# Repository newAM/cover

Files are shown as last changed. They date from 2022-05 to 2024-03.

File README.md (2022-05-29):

# Cover

A controller to automate my window shades.

This project is from late 2020; much older than the commit dates indicate.  I revisited it to migrate the raspberry pi controller to NixOS and decided to document the project.

## Software

* [NixOS](https://nixos.org/) for the raspberry pi OS
* [KiCad](https://www.kicad.org/) (version 5) for PCB design
* [OpenSCAD](https://openscad.org/) for 3D printed parts

## Hardware

The hardware consists of:

* A raspberry pi
* A custom pi hat to drive motors
* A motor per shade
* Plastic 3D printed motor mounts
* Metal 3D printed grips
* Plastic 3D printed guides
* 2 reed switches on each shade for endstops

### Shades

The shades on my windows have a continuous ball chain string without any clasps.  The ball chain originally had some plastic stoppers on them, but these all broke off before this project due to UV exposure.

The windows have a clutch on them, I measured the force required to overcome this clutch by tieing a water bottle onto the ball chain, and filling it with water until the chain started to move.  The final weight of the water bottle was 2 kilos ∴ about 20N of force is required to move the shades.

### Motors

I purchased generic 12V motors online, if you search "DC 12V worm gear motor" you will find these easily at almost every retailer.  These had more than enough torque to overcome the 20N of the clutch.

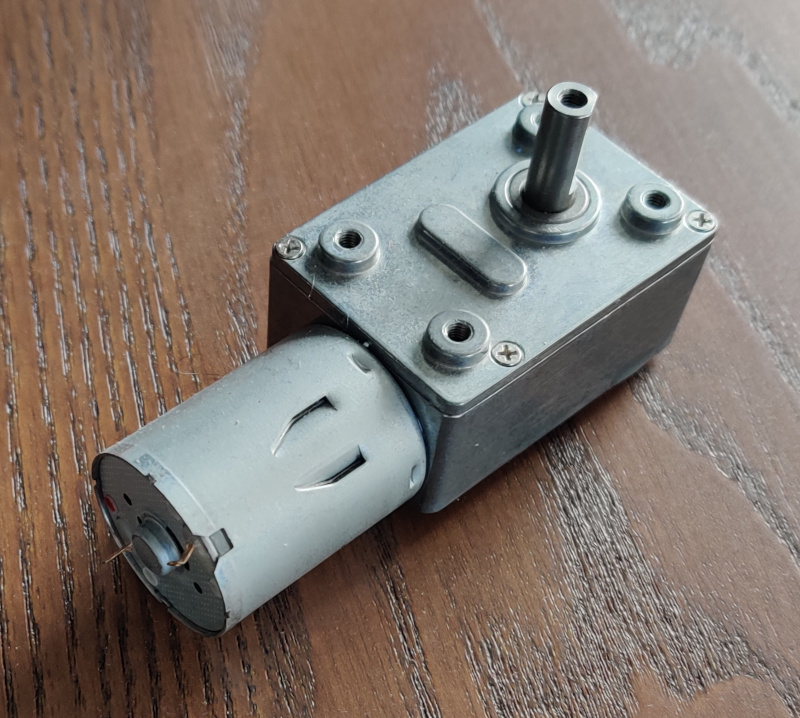
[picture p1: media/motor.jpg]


I purchased 25 rpm motors, which was lower than I needed.  The grips ended up being a smaller diameter than I initially intended; which means the shades move slower than intended.

#### Grips

The grip is a metal 3D printed part with grooves for the ball chain.  I tried to make this in plastic, but the forces required always stripped plastic parts.

The intent was to make this part match the diameter of the clutch on my shades, but metal 3D printing is extremely expensive, and I ended up making the part much smaller to keep costs down.  Each part ended up costing $40 from [shapeways](https://www.shapeways.com/).

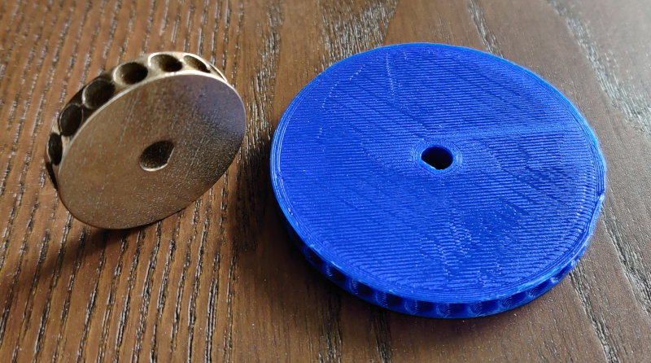
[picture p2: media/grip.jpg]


#### Mount

The mount screws onto the motor and has two large flat surfaces to mount the motor onto the wall with command strips.  I used command strips because I rent, but they were probably the best solution anyway.

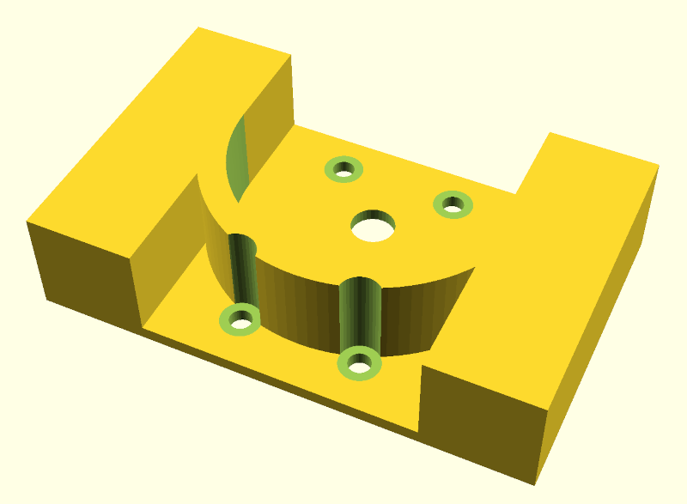
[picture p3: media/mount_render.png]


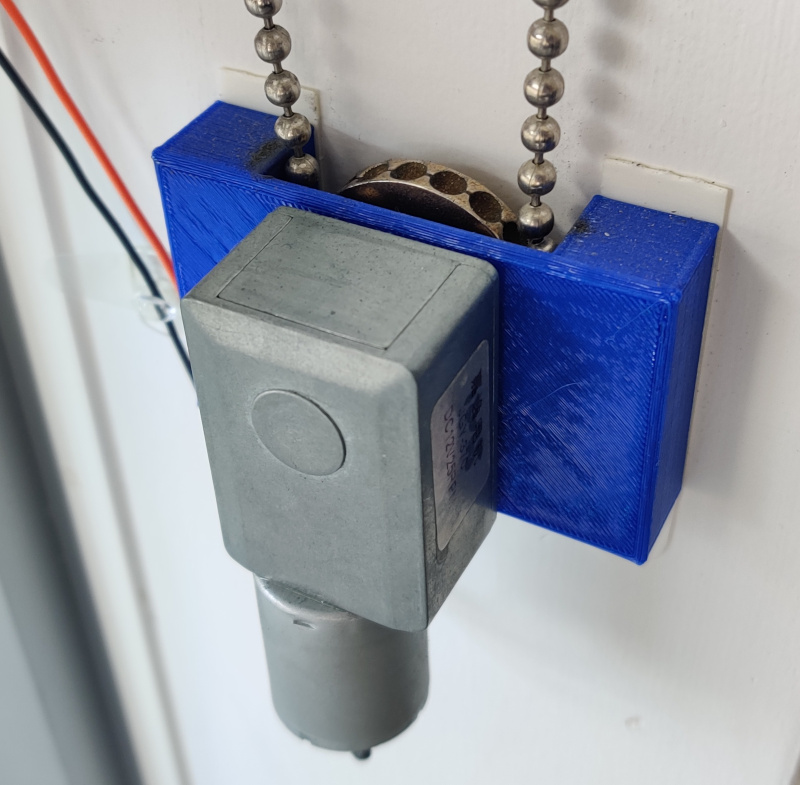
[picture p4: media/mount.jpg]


### Endstops

The endstops consisted of two reed switches per window, one at the top of the frame, and one at the bottom.  I taped magnets onto the shades to trip the reed switches when the shades hit the limit.

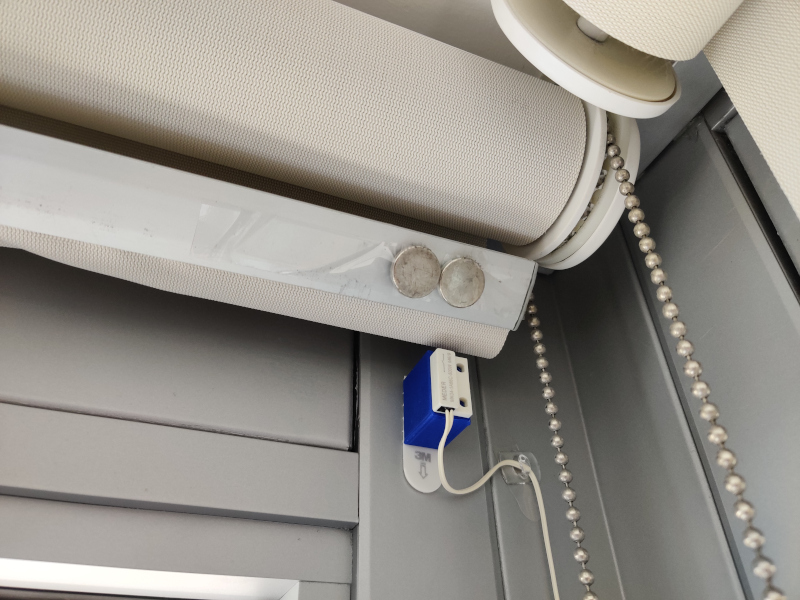
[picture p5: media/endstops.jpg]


3D printed mounts were necessary to raise the reed switches to the shades.

### Controller

The controller is just a hat on a raspberry pi with 6x inputs for reed switches, and 3x DRV8871DDAR motor drivers for the output.

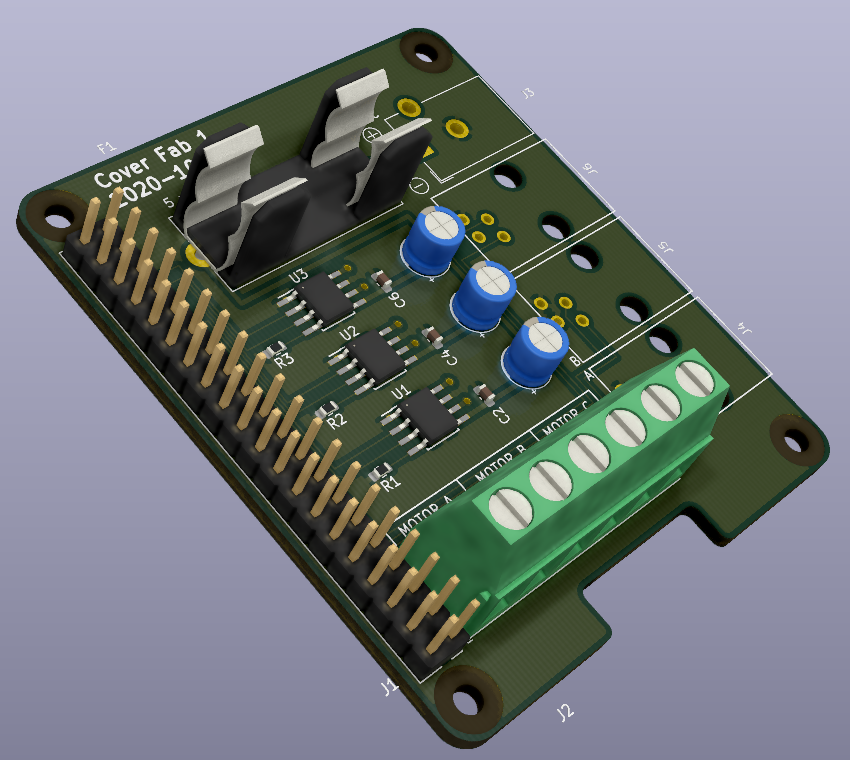
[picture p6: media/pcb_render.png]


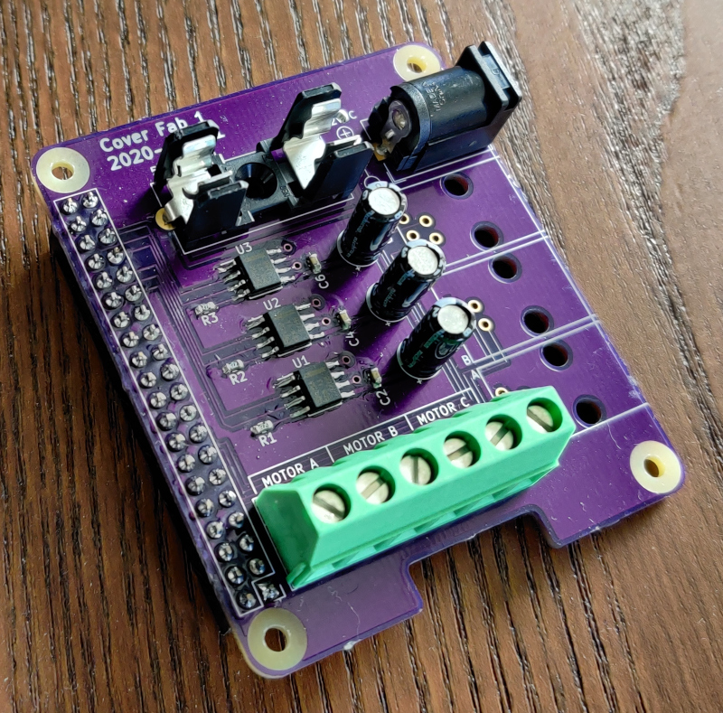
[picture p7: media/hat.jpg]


If I had to do this project over I would have used an Ethernet connected microcontroller instead of a pi.  Upon boot the raspberry pi takes a few seconds to apply the GPIO configuration in `/boot/config.txt`, which is not desirable, as this can lead to the shades moving beyond their endstop positions.

The controller takes commands over MQTT for move up, move down, and stop.

I run [NixOS](https://nixos.org/) on the pi.  The only other configuration necessary is putting `gpio=5,12,6,13,19,16=op,dl` into `/boot/config.txt`:

```nix
{
  boot.loader.raspberryPi = {
    enable = true;
    version = n;
    firmwareConfig = ''
      gpio=5,12,6,13,19,16=op,dl
    '';
  };
}
```

The service is a simple python script that I am not very proud of because it is all blocking code with polling.  I plan to rewrite this at some point, but it keeps working so I keep putting it off.

## Home Assistant

Home-assistant has a [MQTT cover integration](https://www.home-assistant.io/integrations/cover.mqtt/) that works out of the box.

```nix
{
  services.home-assistant.config.cover = [
    {
      platform = "mqtt";
      name = "Middle Window";
      unique_id = "middle_window";
      command_topic = "/home/sunroom/middle_window/set";
      position_topic = "/home/sunroom/middle_window/position";
      optimistic = false;
      retain = false;
    }
    # ... other shades
  ];
}
```

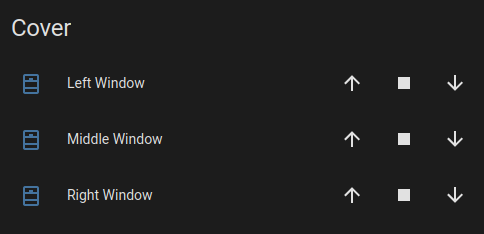
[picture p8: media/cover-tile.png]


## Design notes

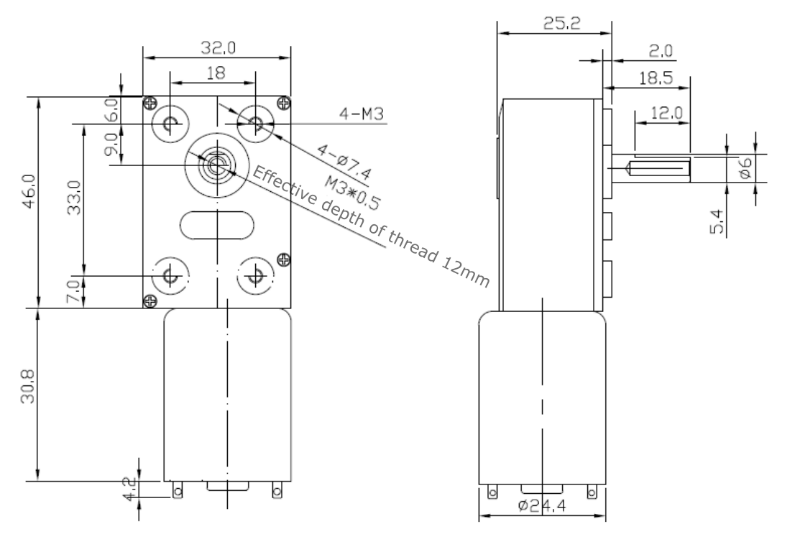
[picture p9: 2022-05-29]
media/motor_dimensions.png

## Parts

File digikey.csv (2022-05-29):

Index | Quantity | Part Number | Manufacturer Part Number | Description | Customer Reference | Available | Backorder | Unit Price | Extended Price CAD
1 | 2 | 277-8599-ND | 1715190 | TERM BLK 6POS SIDE ENTRY 5MM PCB |  | 2 | 0 | 5.26000 | 10.52
2 | 6 | 296-43024-1-ND | DRV8871DDAR | IC MOTOR DRVR UNIPLR 8SO PWRPAD |  | 6 | 0 | 3.86000 | 23.16
3 | 6 | 493-1121-ND | UVR1J220MDD | CAP ALUM 22UF 20% 63V RADIAL |  | 6 | 0 | 0.32000 | 1.92
4 | 10 | 1276-1934-1-ND | CL10B104KB8NFNC | CAP CER 0.1UF 50V X7R 0603 |  | 10 | 0 | 0.04000 | 0.40
5 | 2 | 486-1258-ND | 0031.8201 | FUSE BLOK CARTRIDGE 500V 10A PCB |  | 2 | 0 | 1.40000 | 2.80
6 | 2 | 507-1227-ND | 5SF 1.6-R | FUSE GLASS 1.6A 250VAC 5X20MM |  | 2 | 0 | 0.35000 | 0.70
7 | 2 | CP-102AH-ND | PJ-102AH | CONN PWR JACK 2X5.5MM SOLDER |  | 2 | 0 | 1.10000 | 2.20
8 | 12 | AE11234-ND | A-20040 | CONN MOD JACK 4P4C R/A UNSHLD |  | 12 | 0 | 0.95800 | 11.50
9 | 25 | AE10314-ND | A-MO 4/4 F50 | CONN MOD PLUG 4P4C UNSHIELDED |  | 25 | 0 | 0.19880 | 4.97
10 | 2 | Q1182-ND | QFWB-30-12-US01 | AC/DC WALL MOUNT ADAPTER 12V 30W |  | 2 | 0 | 12.92000 | 25.84
11 | 2 | S7123-ND | PPPC202LFBN-RC | CONN HDR 40POS 0.1 GOLD PCB |  | 2 | 0 | 3.44000 | 6.88
12 | 2 | 507-1246-ND | 5ST 1-R | FUSE GLASS 1A 250VAC 5X20MM |  | 2 | 0 | 0.35000 | 0.70
13 | 2 | 507-1248-ND | 5ST 1.6-R | FUSE GLASS 1.6A 250VAC 5X20MM |  | 2 | 0 | 0.35000 | 0.70
14 | 10 | 469-1039-ND | 8110 | MAGNET 1" L X 0.25" W RECT |  | 10 | 0 | 1.22000 | 12.20
15 | 10 | 311-27.0KHRCT-ND | RC0603FR-0727KL | RES SMD 27K OHM 1% 1/10W 0603 |  | 10 | 0 | 0.03200 | 0.32
16 | 10 | 311-4.70KHRCT-ND | RC0603FR-074K7L | RES SMD 4.7K OHM 1% 1/10W 0603 |  | 10 | 0 | 0.03200 | 0.32

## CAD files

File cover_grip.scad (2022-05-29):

HEIGHT = 6;
STRING_RADIUS = 0.6;
SHAFT_RADIUS = 3;
FLAT_RADIUS = 2.4;
BEAD_RADIUS = 2.4;
BEAD_GAP = 0.2;
BEAD_SPACING = 6;
NUM_BEADS = 18;

CIRCUMFERENCE = NUM_BEADS * BEAD_SPACING;
RADIUS = CIRCUMFERENCE / (2 * PI);
ANGLE_SPACING = 360 / NUM_BEADS;

echo(CIRCUMFERENCE=CIRCUMFERENCE);
echo(RADIUS=RADIUS);
echo(ANGLE_SPACING=ANGLE_SPACING);

module bead_holes()
{
    fn = 36;
    hole_size = BEAD_RADIUS + BEAD_GAP;
    cyl_radius = RADIUS + hole_size;

    // repeat bead holes
    for (theta=[0:ANGLE_SPACING:360])
    {
        union()
        {
            // cylindrical to Cartesian coordinate conversion
            translate([RADIUS * cos(theta), RADIUS * sin(theta), 0])
            {
                // bead hole
                sphere(hole_size, $fn=fn);
            }
            translate([cyl_radius * cos(theta), cyl_radius * sin(theta), 0])
            {
                rotate([-theta, 90, 0])
                {
                    cylinder(r=hole_size, h=hole_size, $fn=fn);
                }
            }
        }
    }
}

difference()
{
    // body
    cylinder(h=HEIGHT, r1=RADIUS, r2=RADIUS, center=true, $fn=180);

    bead_holes();

    // string cutout
    difference()
    {
        linear_extrude(height=STRING_RADIUS+BEAD_GAP, center=true)
        {
            difference()
            {
                circle(r=RADIUS+0.001, $fn=180);
                circle(r=RADIUS-STRING_RADIUS+BEAD_GAP, $fn=180);
            }
        }
        bead_holes();
    }

    // shaft
    linear_extrude(height=HEIGHT+1, center=true)
    {
        scale(1.1)
        {
            difference()
            {
                circle(r=SHAFT_RADIUS, $fn=90);

                // "D" shape
                translate([FLAT_RADIUS + SHAFT_RADIUS, 0, 0])
                {
                    square([SHAFT_RADIUS * 2, SHAFT_RADIUS * 2], center=true);
                }
            }
        }
    }
}

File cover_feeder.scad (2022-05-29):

GEARBOX_WIDTH = 32;
GEARBOX_DEPTH = 46;
GEARBOX_HEIGHT = 25.2;

GEARBOX_GAP = 1;

SCREW_HOLE_HEIGHT = 2;
SCREW_HOLE_X_OFFSET = 9;
SCREW_HOLE_Y_OFFSET_TOP = 17;
SCREW_HOLE_Y_OFFSET_BOTTOM = 16;

CASE_WALL_THICKNESS = 2;
GAP_SIZE = 0.3;  // gap between motor and housing

SHAFT_Y_OFFSET = 8;
SHAFT_DIAMETER = 6;
SHAFT_LENGTH = 14;
SHAFT_CLEARANCE = 2;

M3_HOLE_DIAMETER = 3.3;
M3_SCREW_HEAD_DIAMETER = 6;

GRIP_DIAMETER = 41;
GRIP_GUIDE_WALL_THICKNESS = 4;
GRIP_GUIDE_DEPTH = 12;
GRIP_GUIDE_HEIGHT = SHAFT_LENGTH - CASE_WALL_THICKNESS + SHAFT_CLEARANCE;
GRIP_OD = GRIP_DIAMETER + GRIP_GUIDE_WALL_THICKNESS * 2;

COMMAND_STRIP_LENGTH = 46;
COMMAND_STRIP_WIDTH = 16;

module m3_cutout()
{
    cylinder(
        h=CASE_WALL_THICKNESS + 0.001,
        d=M3_HOLE_DIAMETER,
        center=true,
        $fn=36
    );
    translate([0, 0, CASE_WALL_THICKNESS / 2 + GRIP_GUIDE_HEIGHT / 2])
    {
        cylinder(
            h=GRIP_GUIDE_HEIGHT + 0.001,
            d=M3_SCREW_HEAD_DIAMETER,
            center=true,
            $fn=36
        );
    }
}

module feeder()
{
    union()
    {
        difference()
        {
            // ring
            cylinder(
                h=GRIP_GUIDE_HEIGHT,
                d=GRIP_OD,
                $fn=100,
                center=true
            );
            cylinder(h=GRIP_GUIDE_HEIGHT+0.001, d=GRIP_DIAMETER, $fn=100, center=true);

            // half-cylinder
            translate([0, GRIP_OD / 2, 0])
            {
                cube(GRIP_OD, center=true);
            }

        }

        // straight portion
        for (x=[1, -1])
        {
            translate(
                [
                    (GRIP_DIAMETER / 2 + GRIP_GUIDE_WALL_THICKNESS / 2) * x,
                    GRIP_GUIDE_DEPTH / 2,
                    0,
                ]
            )
            {
                cube(
                    [
                        GRIP_GUIDE_WALL_THICKNESS,
                        GRIP_GUIDE_DEPTH,
                        GRIP_GUIDE_HEIGHT
                    ],
                    center=true
                );
            }
        }
    }
}

difference()
{
    base_width = GRIP_DIAMETER + COMMAND_STRIP_WIDTH * 2;

    union()
    {
        cube(
            [
                base_width,
                GEARBOX_DEPTH,
                CASE_WALL_THICKNESS
            ],
            center=true
        );
        translate(
            [
                0,
                SHAFT_Y_OFFSET,
                CASE_WALL_THICKNESS / 2 + GRIP_GUIDE_HEIGHT / 2
            ]
        )
        {
            feeder();
        }

        for (x=[1, -1])
        {
            translate(
                [
                    x * ((GRIP_DIAMETER + COMMAND_STRIP_WIDTH) / 2),
                    0,
                    (CASE_WALL_THICKNESS + GRIP_GUIDE_HEIGHT) / 2,
                ]
            )
            {
                cube(
                    [COMMAND_STRIP_WIDTH, COMMAND_STRIP_LENGTH, GRIP_GUIDE_HEIGHT],
                    center=true
                );
            }
        }
    }
    translate([0, SHAFT_Y_OFFSET, 0])
    {
        cylinder(
            h=CASE_WALL_THICKNESS + 0.001,
            d=SHAFT_DIAMETER + GAP_SIZE * 2,
            center=true,
            $fn=36
        );
    }
    for (x=[1, -1])
    {
        translate([x*SCREW_HOLE_X_OFFSET, SCREW_HOLE_Y_OFFSET_TOP, 0])
        {
            m3_cutout();
        }
        translate([x*SCREW_HOLE_X_OFFSET, -SCREW_HOLE_Y_OFFSET_BOTTOM, 0])
        {
            m3_cutout();
        }
    }
}

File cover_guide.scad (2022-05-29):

WIDTH = 17;
LENGTH = 60;
HEIGHT = 60;

difference() {
    cylinder(WIDTH, LENGTH, LENGTH, $fn=3, center=false);
    translate([-100, 0, -0.001]) {
        cube([LENGTH * 100, LENGTH * 100, LENGTH * 100]);
    }
}

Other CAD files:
reed_holder.scad

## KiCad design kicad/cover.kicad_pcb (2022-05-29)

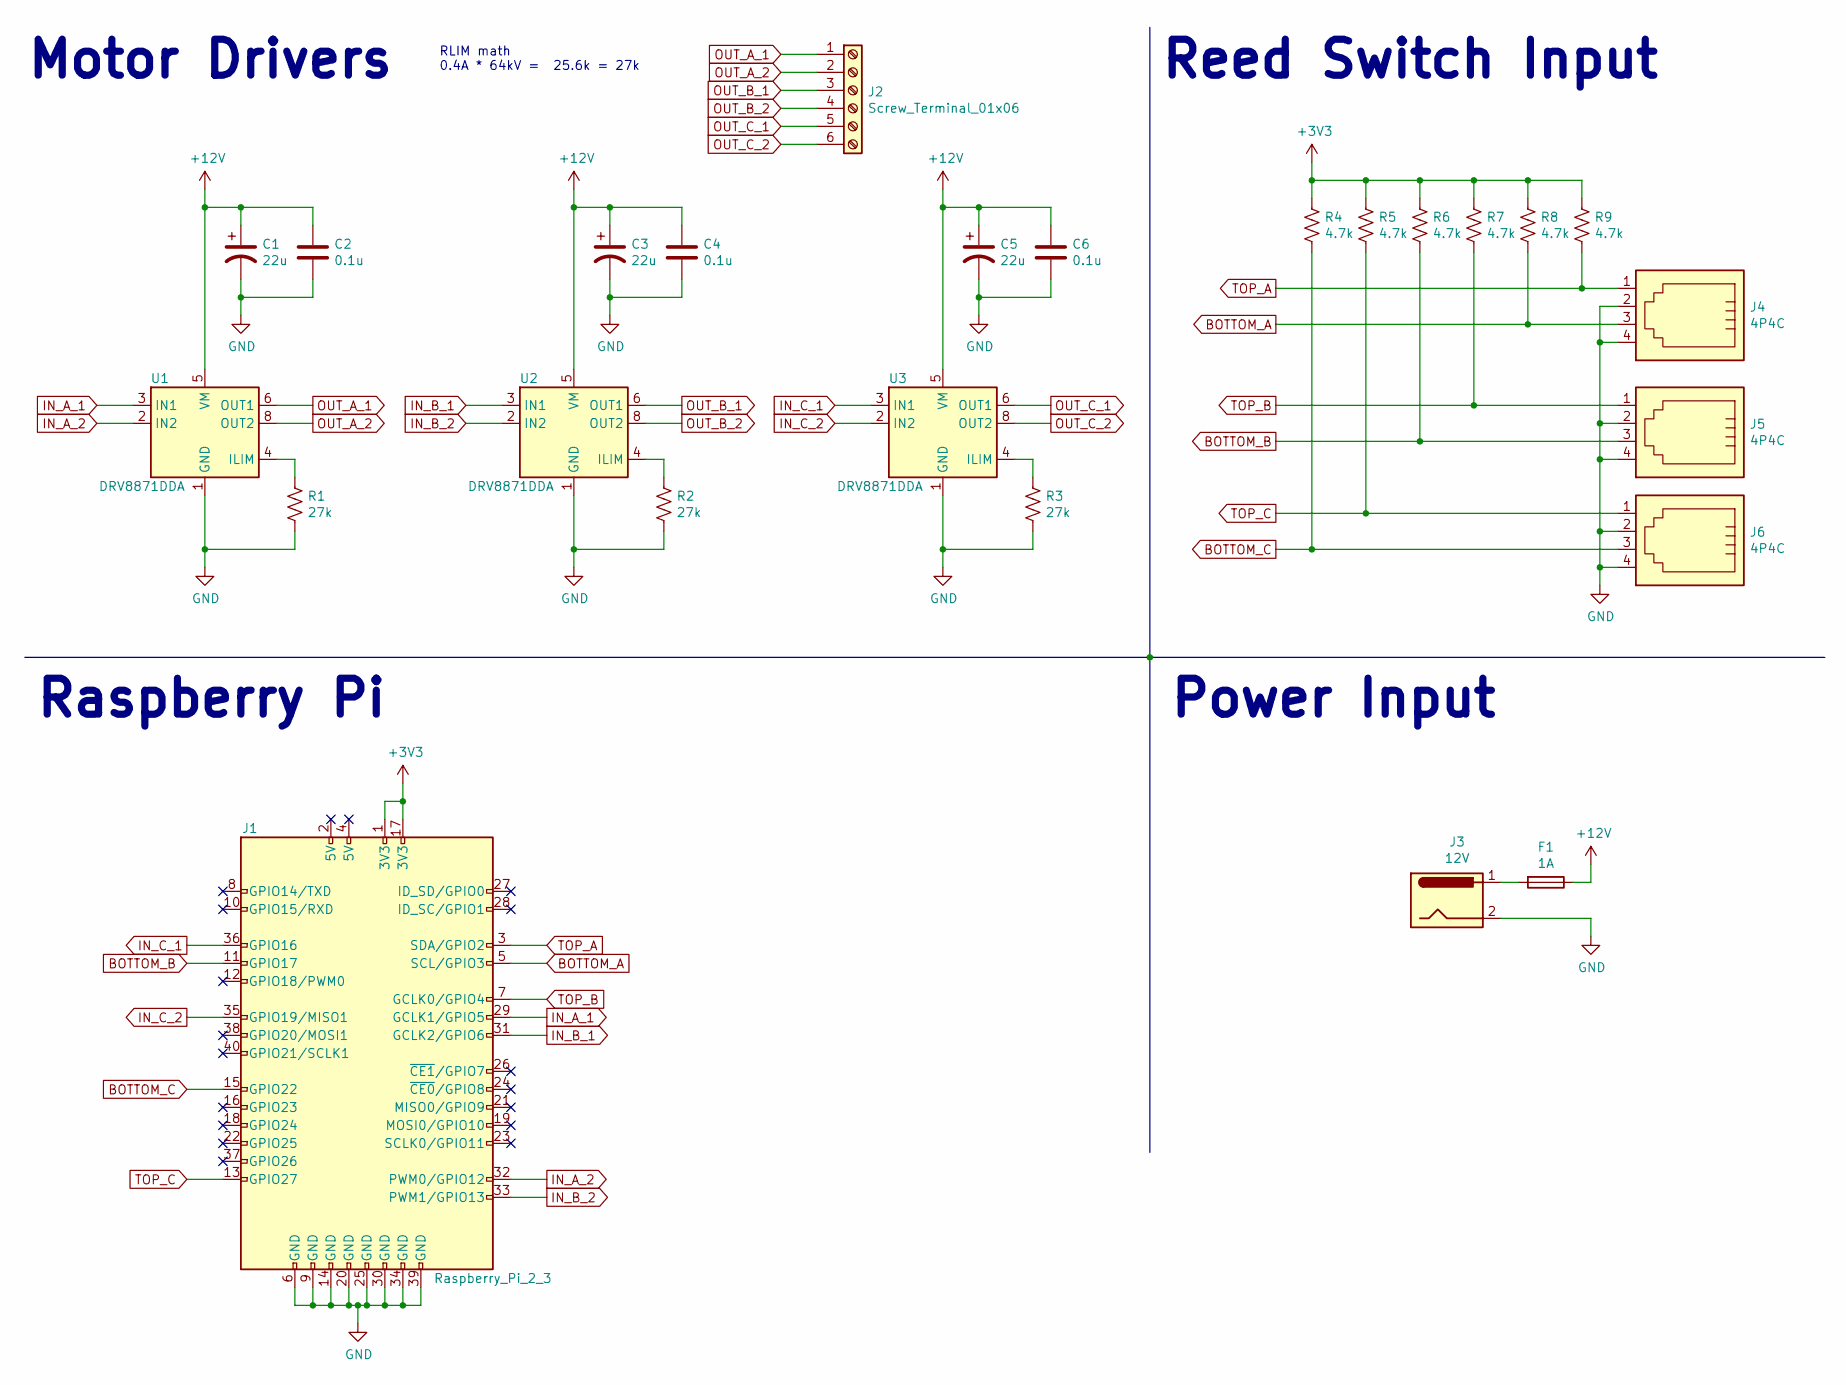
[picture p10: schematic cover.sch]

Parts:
C1, C3, C5: 22u; CP_Radial_D5.0mm_P2.00mm
C2, C4, C6: 0.1u; C_0603_1608Metric
F1: 1A; Fuseholder_Cylinder-5x20mm_Schurter_0031_8201_Horizontal_Op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
J1: Raspberry_Pi_2_3; PinHeader_2x20_P2.54mm_Vertical
J2: Screw_Terminal_01x06; TerminalBlock_Phoenix_MKDS-1,5-6_1x06_P5.00mm_Horizontal
J3: 12V; BarrelJack_CUI_PJ-102AH_Horizontal
J4, J5, J6: 4P4C; A-2004-3-4-LP-N-R
R1, R2, R3: 27k; R_0603_1608Metric
R4, R5, R6, R7, R8, R9: 4.7k; R_0603_1608Metric
U1, U2, U3: DRV8871DDA; Texas_HTSOP-8-1EP_3.9x4.9mm_P1.27mm_EP2.95x4.9mm_Mask2.4x3.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

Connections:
+3V3: J1.1 (3V3), J1.17 (3V3), R4.1, R5.1, R6.1, R7.1, R8.1, R9.1
+12V: C1.1, C2.1, C3.1, C4.1, C5.1, C6.1, F1.1, U1.5 (VM), U2.5 (VM), U3.5 (VM)
BOTTOM_A: J1.5 (SCL/GPIO3), J4.3, R8.2
BOTTOM_B: J1.11 (GPIO17), J5.3, R6.2
BOTTOM_C: J1.15 (GPIO22), J6.3, R4.2
GND: C1.2, C2.2, C3.2, C4.2, C5.2, C6.2, J1.6 (GND), J1.9 (GND), J1.14 (GND), J1.20 (GND), J1.25 (GND), J1.30 (GND), J1.34 (GND), J1.39 (GND), J3.2, J4.2, J4.4, J5.2, J5.4, J6.2, J6.4, R1.2, R2.2, R3.2, U1.1 (GND), U1.7 (GND), U1.9 (GND), U2.1 (GND), U2.7 (GND), U2.9 (GND), U3.1 (GND), U3.7 (GND), U3.9 (GND)
IN_A_1: J1.29 (GCLK1/GPIO5), U1.3 (IN1)
IN_A_2: J1.32 (PWM0/GPIO12), U1.2 (IN2)
IN_B_1: J1.31 (GCLK2/GPIO6), U2.3 (IN1)
IN_B_2: J1.33 (PWM1/GPIO13), U2.2 (IN2)
IN_C_1: J1.36 (GPIO16), U3.3 (IN1)
IN_C_2: J1.35 (GPIO19/MISO1), U3.2 (IN2)
unnamed: F1.2, J3.1
unnamed: R1.1, U1.4 (ILIM)
unnamed: R2.1, U2.4 (ILIM)
unnamed: R3.1, U3.4 (ILIM)
OUT_A_1: J2.1, U1.6 (OUT1)
OUT_A_2: J2.2, U1.8 (OUT2)
OUT_B_1: J2.3, U2.6 (OUT1)
OUT_B_2: J2.4, U2.8 (OUT2)
OUT_C_1: J2.5, U3.6 (OUT1)
OUT_C_2: J2.6, U3.8 (OUT2)
TOP_A: J1.3 (SDA/GPIO2), J4.1, R9.2
TOP_B: J1.7 (GCLK0/GPIO4), J5.1, R7.2
TOP_C: J1.13 (GPIO27), J6.1, R5.2

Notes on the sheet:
RLIM math 0.4A * 64kV = 25.6k = 27k
Motor Drivers
Reed Switch Input
Raspberry Pi
Power Input

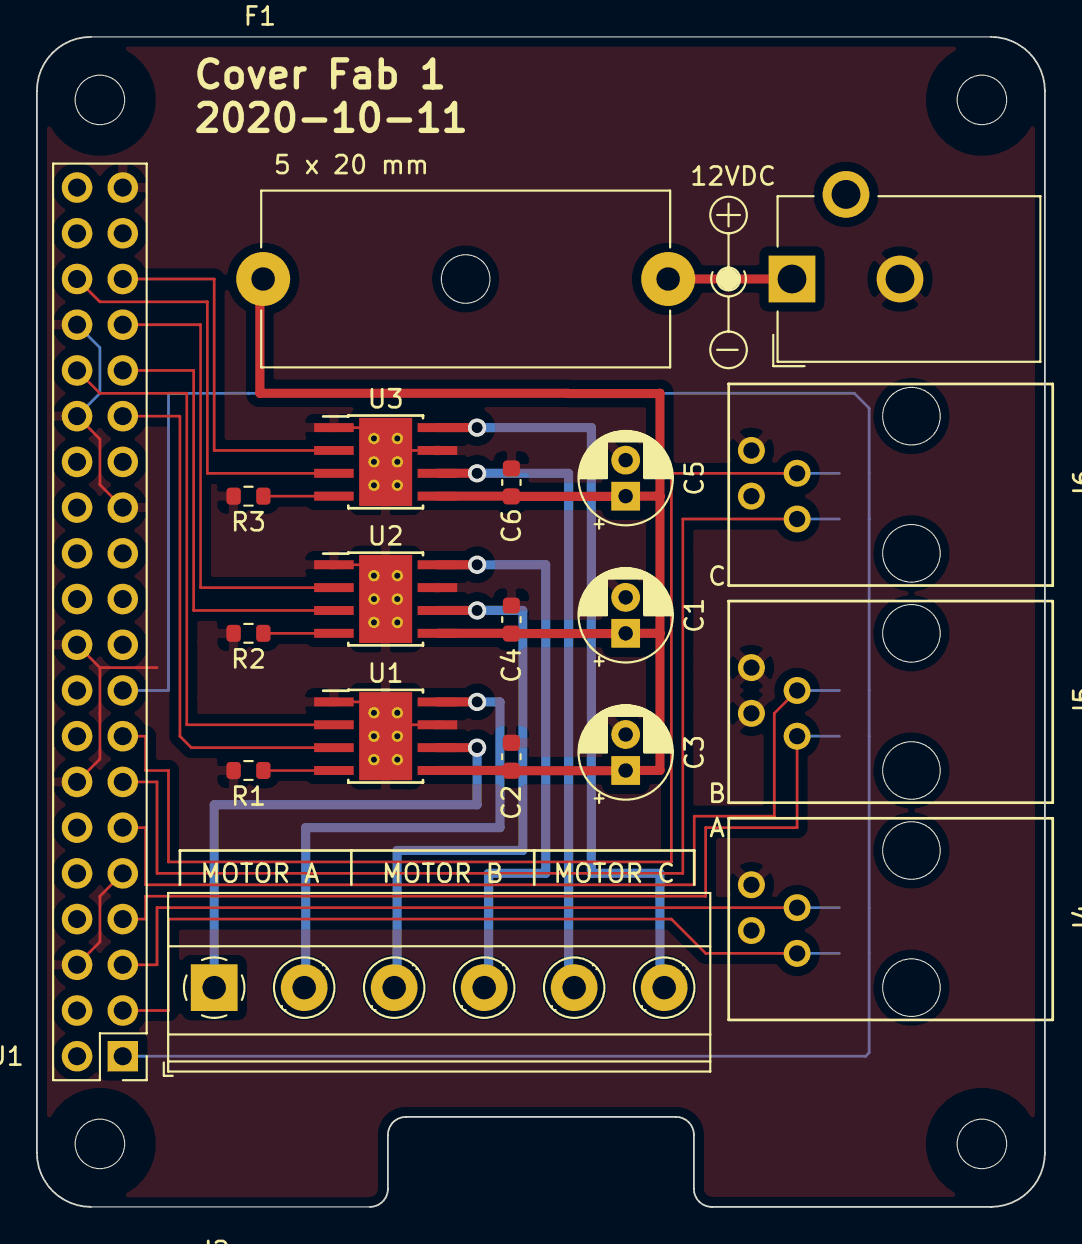
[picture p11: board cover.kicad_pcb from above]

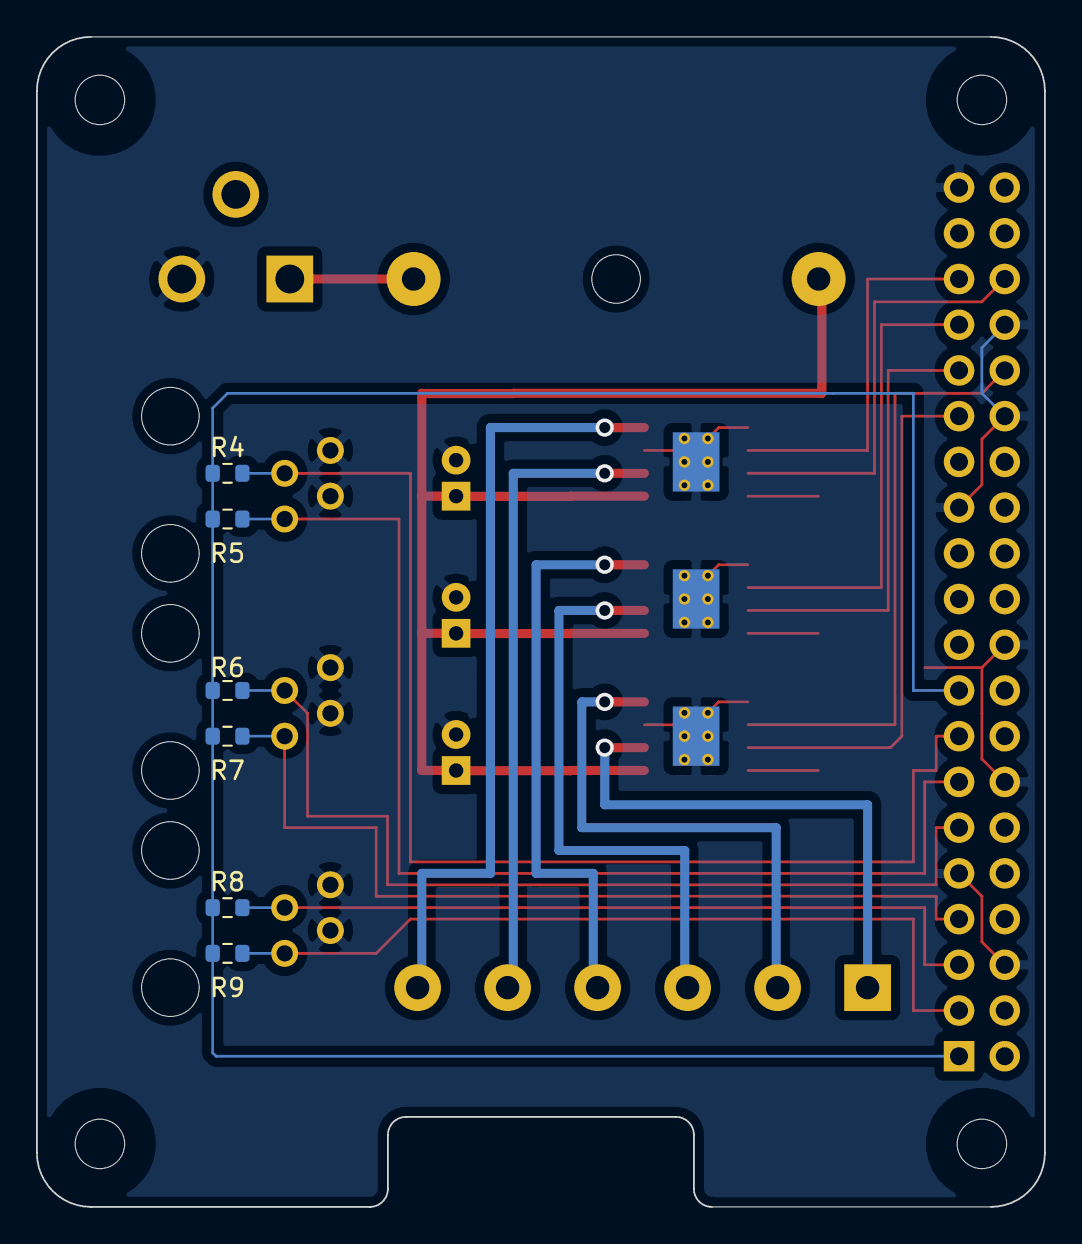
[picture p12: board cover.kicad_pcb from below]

Board: 2 copper layers, 56.0 x 65.0 mm, 25 parts (6 on the bottom side), 25 nets.

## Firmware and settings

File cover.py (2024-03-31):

#!/usr/bin/env python3

""" Cover controller script. """

from gpiozero import LED, Button
from systemd.journal import JournalHandler
from typing import List
from typing import Optional
from typing import Tuple
import argparse
import functools
import logging
import logging.handlers
import paho.mqtt.client as mqtt
import posixpath
import queue
import ssl
import sys
import time

logger = logging.getLogger(__name__)

PAYLOAD_UP: str = "OPEN"
PAYLOAD_DOWN: str = "CLOSE"
PAYLOAD_STOP: str = "STOP"

STATE_CLOSED: str = "closed"
STATE_CLOSING: str = "closing"
STATE_ERROR: str = "error"
STATE_INITIAL: str = "initial"
STATE_OPEN: str = "open"
STATE_OPENING: str = "opening"
STATE_PARTIAL: str = "partial"


class Cover:
    """
    Represents a single cover.

    One cover is a shade that has a motor with an H-bridge, with two GPIOs
    outputs connected to the H-bridge and two GPIO inputs connected to switches
    that indicate the limits.

    Each motor attached to the cover has three states:

        * Opening
        * Closing
        * Stopped

    From these motor states and the switches each cover derives several more
    states:

        * Open
        * Closed
        * Opening
            * if top switch is set -> Open
            * if state is Opening for more than 70s -> Error
            * if both switches are set -> Error
        * Unknown
            * if top switch is set -> Open
            * if bottom switch is set -> Closed
            * if both switches are set -> Error
        * Error
    """

    class _LoggerAdapter(logging.LoggerAdapter):
        """Prepends the context onto logging messages."""

        def process(self, msg: str, kwargs: dict) -> Tuple[str, dict]:
            return f"[{self.extra['base_topic']}] {msg}", kwargs

    def __init__(
        self,
        *,
        up_motor_pin: int,
        down_motor_pin: int,
        up_limit_pin: int,
        down_limit_pin: int,
        up_time_limit: float,
        down_time_limit: float,
        base_topic: str,
        client: mqtt.Client,
    ):
        self.logger = self._LoggerAdapter(
            logger=logging.getLogger(__name__),
            extra={"base_topic": base_topic},
        )

        self.up_motor = LED(up_motor_pin)
        self.down_motor = LED(down_motor_pin)
        self.lower_limit = Button(down_limit_pin)
        self.upper_limit = Button(up_limit_pin)
        self.down_time_limit = down_time_limit
        self.up_time_limit = up_time_limit
        self.set_topic = posixpath.join(base_topic, "set")
        self.position_topic = posixpath.join(base_topic, "position")

        self.client = client
        self.queue = queue.Queue()
        self._state_start = time.monotonic()
        self._state: str = STATE_INITIAL
        self._postion: Optional[float] = None

        self.motor_stop()

    def get_state(self) -> str:
        """Get the current cover state."""
        return self._state

    def state_elapsed(self) -> float:
        """Get the duration in seconds of the current state."""
        return time.monotonic() - self._state_start

    def set_state(self, state: str):
        """Set the current cover state."""
        elapsed = self.state_elapsed()
        self.logger.debug(
            f"Changing state from {self._state} to {state} "
            f"after {elapsed:.3f}s"
        )

        if self._state == STATE_OPENING:
            self.up_motor.off()
            self.down_motor.on()
            time.sleep(0.12)
            self.down_motor.off()
        elif self._state == STATE_CLOSING:
            self.down_motor.off()
            self.up_motor.on()
            time.sleep(0.12)
            self.up_motor.off()

        if (
            state not in {STATE_OPEN, STATE_CLOSED}
            and self._postion is not None
        ):
            if self._state == STATE_OPENING:
                self._postion += elapsed * (100 / self.up_time_limit)
                self._postion = min(self._postion, 99)
            elif self._state == STATE_CLOSING:
                self._postion -= elapsed * (100 / self.down_time_limit)
                self._postion = max(self._postion, 1)

            self.publish_position()

        self._state = state
        self._state_start = time.monotonic()

    def publish_position(self):
        if self._postion is not None:
            p = str(int(self._postion))
            self.logger.debug(f"publishing {p}")
            self.client.publish(self.position_topic, p)

    def get_payload(self) -> Optional[str]:
        """Gets a payload from the queue if avaliable."""
        try:
            payload = self.queue.get_nowait()
        except queue.Empty:
            return None
        else:
            self.logger.debug(f"new payload: {payload}")
            return payload

    def state_closing(self):
        if self.lower_limit.is_pressed:
            self.set_state(STATE_CLOSED)
            return

        self.up_motor.off()
        self.down_motor.on()

        elapsed = self.state_elapsed()
        if elapsed > self.down_time_limit:
            self.logger.info(
                f"{self.get_state()} timeout "
                f"{elapsed} > {self.down_time_limit}"
            )
            self.set_state(STATE_CLOSED)
            return

        payload = self.get_payload()
        if payload == PAYLOAD_UP:
            self.set_state(STATE_OPENING)
        elif payload == PAYLOAD_STOP:
            self.set_state(STATE_PARTIAL)
        elif payload is not None:
            self.logger.info(f"discarding payload: {payload}")

    def state_opening(self):
        if self.upper_limit.is_pressed:
            self.set_state(STATE_OPEN)
            return

        self.down_motor.off()
        self.up_motor.on()

        elapsed = self.state_elapsed()
        if elapsed > self.up_time_limit:
            self.logger.info(
                f"{self.get_state()} timeout "
                f"{elapsed} > {self.up_time_limit}"
            )
            self.set_state(STATE_OPEN)
            return

        payload = self.get_payload()
        if payload == PAYLOAD_DOWN:
            self.set_state(STATE_CLOSING)
        elif payload == PAYLOAD_STOP:
            self.set_state(STATE_PARTIAL)
        elif payload is not None:
            self.logger.info(f"discarding payload: {payload}")

    def state_closed(self):
        self.motor_stop()
        if self._postion != 0.0:
            self._postion = 0.0
            self.publish_position()

        if self.upper_limit.is_pressed:
            self.set_state(STATE_ERROR)
            return

        payload = self.get_payload()
        if payload == PAYLOAD_UP:
            self.set_state(STATE_OPENING)
        elif payload is not None:
            self.logger.info(f"discarding payload: {payload}")

    def state_open(self):
        self.motor_stop()
        if self._postion != 100.0:
            self._postion = 100.0
            self.publish_position()

        if self.lower_limit.is_pressed:
            self.set_state(STATE_ERROR)
            return

        payload = self.get_payload()
        if payload == PAYLOAD_DOWN:
            self.set_state(STATE_CLOSING)
        elif payload is not None:
            self.logger.info(f"discarding payload: {payload}")

    def state_error(self):
        self.motor_stop()
        self.logger.critical("Entered error state, halting execution...")
        sys.exit(1)

    def state_initial(self):
        """Initial state of the cover."""
        self.logger.debug("determining position from initial state")
        self.motor_stop()

        if self.upper_limit.is_pressed and self.lower_limit.is_pressed:
            self.set_state(STATE_ERROR)
        elif self.upper_limit.is_pressed:
            self.set_state(STATE_OPEN)
        elif self.lower_limit.is_pressed:
            self.set_state(STATE_CLOSED)
        else:
            self.set_state(STATE_PARTIAL)

    def state_partial(self):
        self.motor_stop()

        if self.upper_limit.is_pressed and self.lower_limit.is_pressed:
            self.set_state(STATE_ERROR)
        elif self.upper_limit.is_pressed:
            self.set_state(STATE_OPEN)
        elif self.lower_limit.is_pressed:
            self.set_state(STATE_CLOSED)

        payload = self.get_payload()
        if payload == PAYLOAD_UP:
            self.set_state(STATE_OPENING)
        elif payload == PAYLOAD_DOWN:
            self.set_state(STATE_CLOSING)
        elif payload is not None:
            self.logger.info(f"discarding payload: {payload}")

    def handle(self):
        """Function to poll to handle events."""
        state = self.get_state()
        if state == STATE_INITIAL:
            self.state_initial()
        elif state == STATE_PARTIAL:
            self.state_partial()
        elif state == STATE_CLOSED:
            self.state_closed()
        elif state == STATE_OPEN:
            self.state_open()
        elif state == STATE_OPENING:
            self.state_opening()
        elif state == STATE_CLOSING:
            self.state_closing()
        elif state == STATE_ERROR:
            self.state_error()
        else:
            self.logger.error(f"Unknown state: {state}")
            self.set_state(STATE_ERROR)
            self.state_error()

    def motor_stop(self):
        self.up_motor.off()
        self.down_motor.off()


def on_message(client, userdata, msg, covers: List[Cover]):
    topic = msg.topic
    payload = msg.payload.decode("utf-8", errors="backslashreplace")
    logger.debug(f"new message on '{topic}' with payload '{payload}'")
    if payload in {PAYLOAD_UP, PAYLOAD_DOWN, PAYLOAD_STOP}:
        for cover in covers:
            if cover.set_topic == topic:
                cover.queue.put_nowait(payload)
                break
        else:
            logger.warning(f"unknown topic '{topic}' with payload '{payload}'")
    else:
        logger.warning(
            f"unknown message on '{topic}' with payload '{payload}'"
        )


def on_connect(client, userdata, flags, rc, covers: List[Cover]):
    logger.info(f"connected to MQTT server with code {rc}")

    for cover in covers:
        logger.info(f"subscribing to {cover.set_topic}")
        client.subscribe(cover.set_topic)


def start_daemon(hostname: str):
    """Starts the daemonic process."""
    handler = JournalHandler(SYSLOG_IDENTIFIER="cover")
    handler.setLevel(logging.DEBUG)
    formatter = logging.Formatter("[{name}] {message}", style="{")
    handler.setFormatter(formatter)

    root_logger = logging.getLogger()
    root_logger.setLevel(logging.DEBUG)
    root_logger.addHandler(handler)

    logger.debug("logging initialized")

    covers = []
    try:
        client = mqtt.Client(
            # TODO: add for version 2
            # callback_api_version=mqtt.CallbackAPIVersion.VERSION1
        )

        covers = [
            Cover(
                up_motor_pin=5,
                down_motor_pin=12,
                up_limit_pin=2,
                down_limit_pin=3,
                base_topic="/home/sunroom/right_window",
                up_time_limit=69.0,
                down_time_limit=70.0,
                client=client,
            ),
            Cover(
                up_motor_pin=6,
                down_motor_pin=13,
                up_limit_pin=4,
                down_limit_pin=17,
                base_topic="/home/sunroom/middle_window",
                up_time_limit=68.0,
                down_time_limit=70.0,
                client=client,
            ),
            Cover(
                up_motor_pin=19,
                down_motor_pin=16,
                up_limit_pin=27,
                down_limit_pin=22,
                base_topic="/home/sunroom/left_window",
                up_time_limit=78.0,
                down_time_limit=80.0,
                client=client,
            ),
        ]

        client.on_connect = functools.partial(on_connect, covers=covers)
        client.on_message = functools.partial(on_message, covers=covers)
        ssl_context = ssl.SSLContext()
        ssl_context.minimum_version = ssl.TLSVersion.TLSv1_3
        ssl_context.load_verify_locations("/etc/ssl/certs/ca-bundle.crt")
        client.tls_set_context(context=ssl_context)
        client.connect(hostname, 8883)
        client.loop_start()
    except Exception:
        logger.exception("failed to init")
        raise

    try:
        logger.info("Entering handler loop")
        while True:
            for cover in covers:
                cover.handle()
            time.sleep(0.02)
    except Exception:
        logger.exception("unhandled exception")
    finally:
        for cover in covers:
            try:
                cover.motor_stop()
            except BaseException:  # noqa: B036
                logger.exception(f"failed to stop motor for cover={cover}")


def main():
    parser = argparse.ArgumentParser(description="cover daemon")
    parser.add_argument(
        "hostname", type=str, help="MQTT server hostname or IPv4"
    )
    args = parser.parse_args()

    start_daemon(args.hostname)


if __name__ == "__main__":
    main()

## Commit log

2022-08-20 Fix all sorts of problems with a Pi 3B+ on NixOS 22.05
    [cover.py]
2022-10-29 flake.lock: update
    • Updated input 'nixpkgs':
    'github:nixos/nixpkgs/34c5293a71ffdb2fe054eb5288adc1882c1eb0b1' (2022-10-09)
    → 'github:nixos/nixpkgs/448a599c49978c2794401bfc3a2e1fba1a8663be' (2022-10-28)
2022-11-19 flake.lock: update
    'github:nixos/nixpkgs/448a599c49978c2794401bfc3a2e1fba1a8663be' (2022-10-28)
    → 'github:nixos/nixpkgs/52b2ac8ae18bbad4374ff0dd5aeee0fdf1aea739' (2022-11-18)
    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
2023-01-13 flake.lock, poetry.lock: update
    'github:nixos/nixpkgs/b72b8b94cf0c012b0252a9100a636cad69696666' (2022-12-02)
    → 'github:nixos/nixpkgs/6c8644fc37b6e141cbfa6c7dc8d98846c4ff0c2e' (2023-01-11)
    updated setuptools 65.6.3 -> 65.7.0
    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
2023-04-25 flake.lock, poetry.lock: update
    'github:nixos/nixpkgs/6c8644fc37b6e141cbfa6c7dc8d98846c4ff0c2e' (2023-01-11)
    → 'github:nixos/nixpkgs/884ac294018409e0d1adc0cae185439a44bd6b0b' (2023-04-24)
    updated setuptools 67.7.1 -> 67.7.2
    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
2023-06-16 flake.lock: update
    'github:nixos/nixpkgs/884ac294018409e0d1adc0cae185439a44bd6b0b' (2023-04-24)
    → 'github:nixos/nixpkgs/7c67f006ea0e7d0265f16d7df07cc076fdffd91f' (2023-06-15)
    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
2023-07-24 flake.lock: update
    'github:nixos/nixpkgs/7c67f006ea0e7d0265f16d7df07cc076fdffd91f' (2023-06-15)
    → 'github:nixos/nixpkgs/12303c652b881435065a98729eb7278313041e49' (2023-07-22)
    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
2023-08-17 flake.lock: update
    'github:nixos/nixpkgs/12303c652b881435065a98729eb7278313041e49' (2023-07-22)
    → 'github:nixos/nixpkgs/caac0eb6bdcad0b32cb2522e03e4002c8975c62e' (2023-08-16)
    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
2023-08-31 flake.lock: update
    'github:nixos/nixpkgs/caac0eb6bdcad0b32cb2522e03e4002c8975c62e' (2023-08-16)
    → 'github:nixos/nixpkgs/e7f38be3775bab9659575f192ece011c033655f0' (2023-08-30)
    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
2023-10-02 flake.lock: update
    'github:nixos/nixpkgs/e7f38be3775bab9659575f192ece011c033655f0' (2023-08-30)
    → 'github:nixos/nixpkgs/f5892ddac112a1e9b3612c39af1b72987ee5783a' (2023-09-29)
    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
2023-11-01 flake.lock: update
    'github:nixos/nixpkgs/f5892ddac112a1e9b3612c39af1b72987ee5783a' (2023-09-29)
    → 'github:nixos/nixpkgs/0cbe9f69c234a7700596e943bfae7ef27a31b735' (2023-10-29)
    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
2023-11-02 flake.lock: update
    • Updated input 'poetry2nix':
    'github:nix-community/poetry2nix/4099e32cb94b586fd3d213465942111964ff50ff' (2023-11-01)
    → 'github:nix-community/poetry2nix/349143fce1c8c38255fb8a8d99e2c0cd5854889c' (2023-11-02)
2024-02-14 flake.lock: update
    'github:nixos/nixpkgs/0cbe9f69c234a7700596e943bfae7ef27a31b735' (2023-10-29)
    → 'github:nixos/nixpkgs/f9d39fb9aff0efee4a3d5f4a6d7c17701d38a1d8' (2024-02-11)
    'github:nix-community/poetry2nix/349143fce1c8c38255fb8a8d99e2c0cd5854889c' (2023-11-02)
    → 'github:nix-community/poetry2nix/4eb2ac54029af42a001c9901194e9ce19cbd8a40' (2024-02-06)
    • Updated input 'poetry2nix/nix-github-actions':
    'github:nix-community/nix-github-actions/bd5bdbb52350e145c526108f4ef192eb8e554fa0' (2023-09-02)
    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
2024-03-12 flake.lock: update
    'github:nixos/nixpkgs/f9d39fb9aff0efee4a3d5f4a6d7c17701d38a1d8' (2024-02-11)
    → 'github:nixos/nixpkgs/3030f185ba6a4bf4f18b87f345f104e6a6961f34' (2024-03-09)
    'github:nix-community/poetry2nix/4eb2ac54029af42a001c9901194e9ce19cbd8a40' (2024-02-06)
    → 'github:nix-community/poetry2nix/3c92540611f42d3fb2d0d084a6c694cd6544b609' (2024-02-22)
    • Updated input 'poetry2nix/flake-utils':
    'github:numtide/flake-utils/ff7b65b44d01cf9ba6a71320833626af21126384' (2023-09-12)
    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
2024-05-20 poetry.lock, flake.lock: update
    updated setuptools 69.2.0 -> 69.5.1
    updated zipp 3.18.1 -> 3.18.2
    'github:nixos/nixpkgs/d8fe5e6c92d0d190646fb9f1056741a229980089' (2024-03-29)
    → 'github:nixos/nixpkgs/6c0b7a92c30122196a761b440ac0d46d3d9954f1' (2024-05-19)
    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
2024-09-12 flake.lock, poetry.lock: update
    'github:nixos/nixpkgs/6c0b7a92c30122196a761b440ac0d46d3d9954f1' (2024-05-19)
    → 'github:nixos/nixpkgs/1355a0cbfeac61d785b7183c0caaec1f97361b43' (2024-09-10)
    updated setuptools 69.5.1 -> 74.1.2
    updated zipp 3.18.2 -> 3.20.1
    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
